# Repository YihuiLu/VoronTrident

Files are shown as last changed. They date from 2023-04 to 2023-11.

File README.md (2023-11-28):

# 一灰VoronTrident省心方案

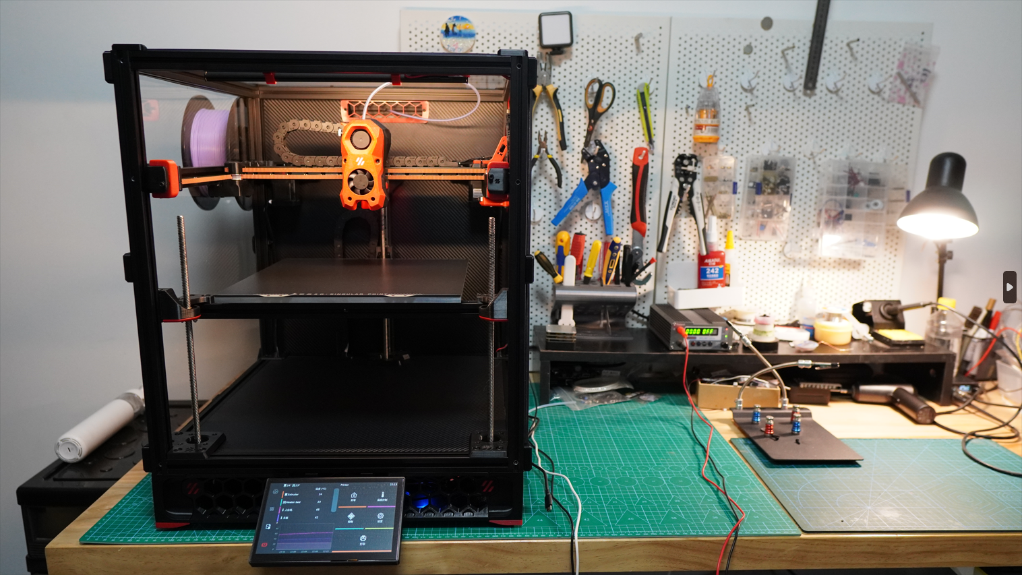
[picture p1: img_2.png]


>### **视频来源**：[Bilibili@我是小一灰](https://www.bilibili.com/video/BV1Na4y1G7fo "我是小一灰")
>### QQ交流群：940677189（满）、339148314（2群）
> ### **Gitee（国内）项目地址**：[VoronTrident省心方案](https://gitee.com/yifeilu/voron-trident "我是小一灰")
> ### **Github项目地址**：[VoronTrident省心方案](https://github.com/YihuiLu/VoronTrident "我是小一灰")

## 方案介绍：
一个被800+人选择的Voron三叉戟装配方案，所有搭配、升级方案都经过挑选和论证，也很容易买到，可以帮助你用更低的成本装出一个高性价比的Voron三叉戟，并有三个预算区间可选。

## 其他资料：
#### **中文安装文档（人工翻译）**：云盘内寻找，太大了Github传不上来

#### **BOM单**：[【腾讯文档】三叉戟BOM](https://docs.qq.com/sheet/DYk5tTHBpSEtPbVh6?tab=BB08J2 "我是小一灰")
#### **BOM单**：[【GoogleDrive】三叉戟BOM](https://drive.google.com/drive/folders/1CQs1cbmclPbKJLRexb8YkByajW4hnJqs?usp=sharing "我是小一灰")

#### **资料包下载地址1**：[阿里云盘 | 提取码：f53j](https://www.aliyundrive.com/s/3trxumG1iBN "我是小一灰")
#### **资料包下载地址2**：[百度云盘 | 提取码：ImYH](https://pan.baidu.com/s/1v2R7Pyi2rMt5dJELF42Imw?pwd=ImYH "我是小一灰")
#### **资料包下载地址3**：[一灰博客](https://drive.yifeilu.cn/aliyun/%E8%A7%86%E9%A2%91%E5%85%B1%E4%BA%AB%E6%96%87%E4%BB%B6/%E4%B8%89%E5%8F%89%E6%88%9F "我是小一灰")

#### 主板、驱动散热风扇支架：已上传至本项目"主板散热支架"文件夹。

#### 屏幕支架（百度云）：https://pan.baidu.com/s/19mTuXdeaKCQE-1kaWURAGw 提取码: 2v3t
#### 屏幕支架（GoogleDrive）：https://drive.google.com/file/d/1Th-2ryH3IjCn2Ey7RBrqZtft3pnhlUIA/view?usp=drive_link

##### - ps:中文装配文档在资料包中 -
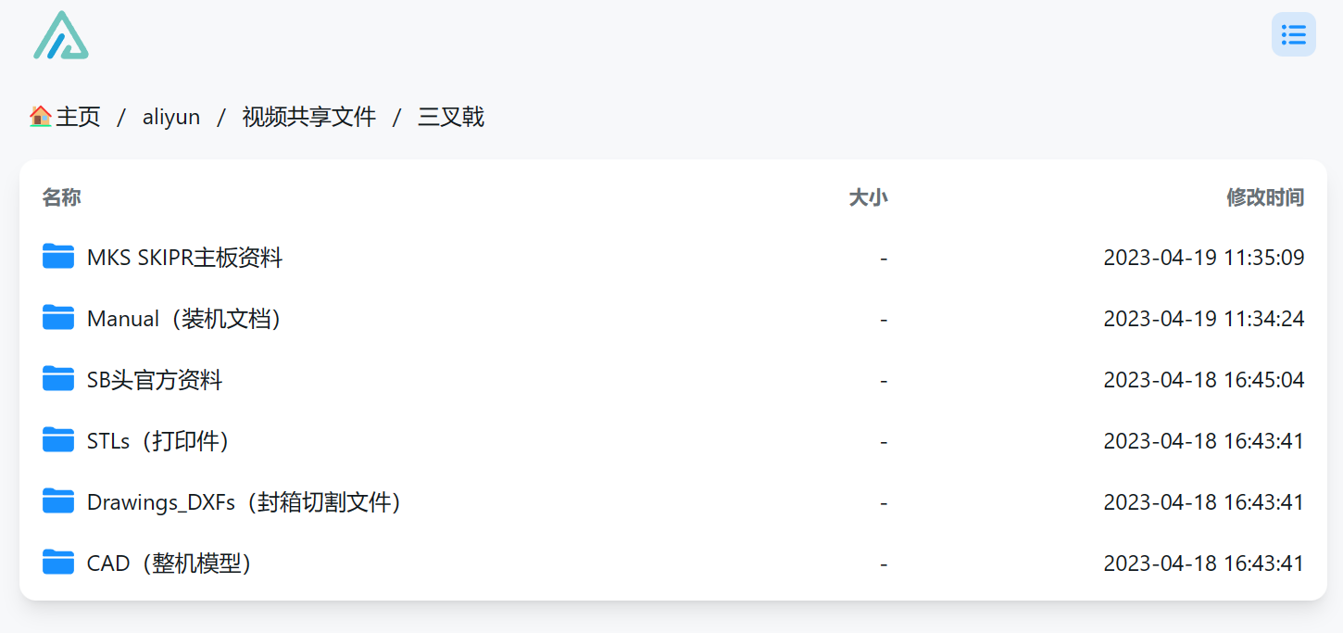
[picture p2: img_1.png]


### **方案中使用到的接线图：**

对于必趣Manta M8P V2.0主板
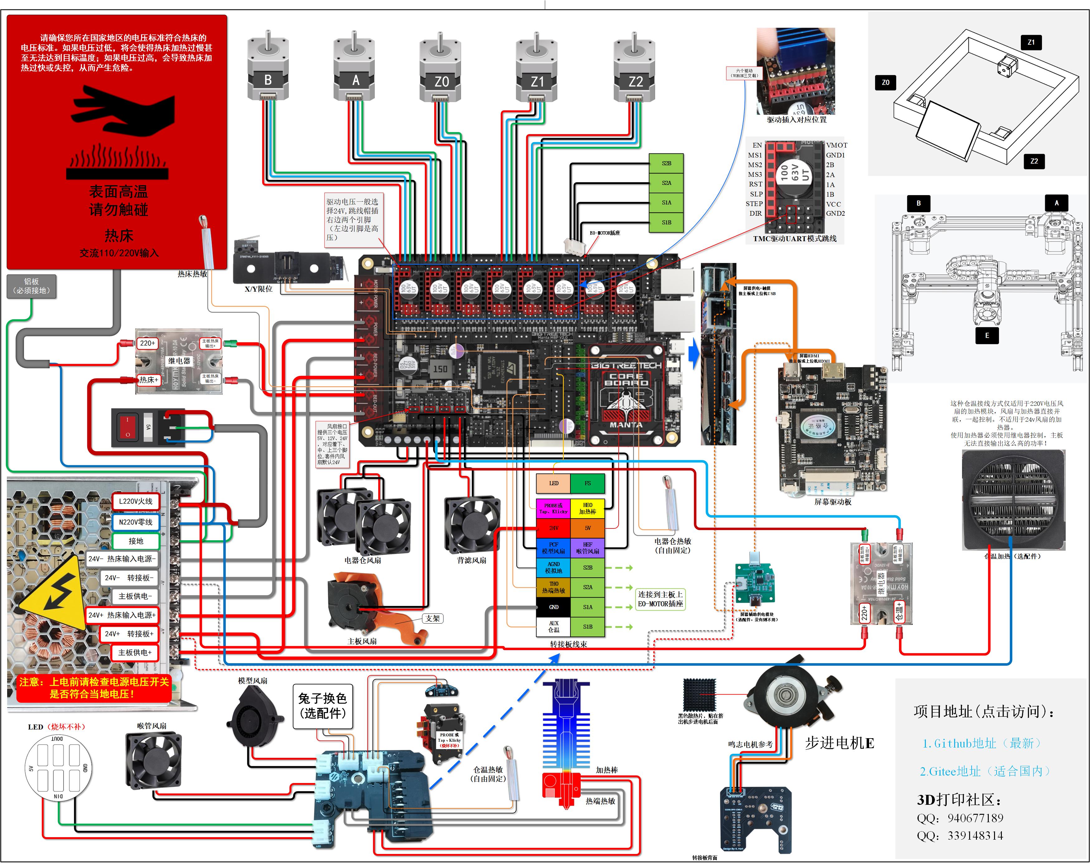
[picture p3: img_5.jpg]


对于必趣Manta M8P V1.1主板
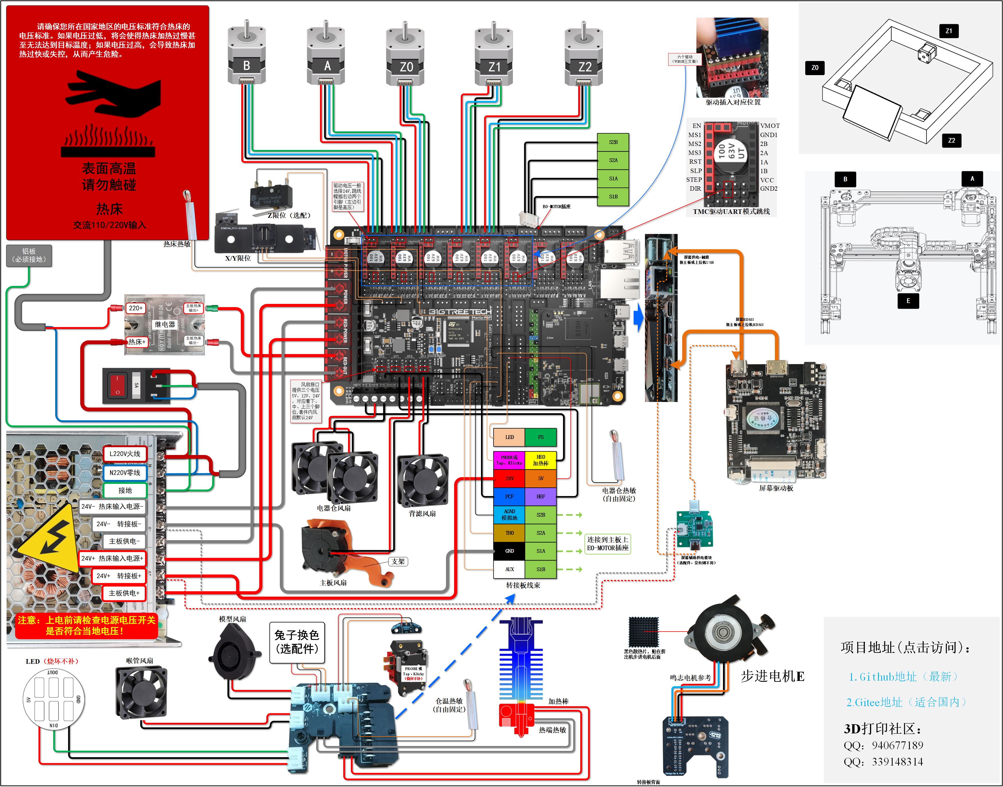
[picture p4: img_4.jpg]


对于MKS Skipr主板

#### **腾讯文档在线查看**：[Voron三叉戟接线图-Skipr](https://docs.qq.com/pdf/DYkhEa2V5WHFHUHd1? "我是小一灰")
#### **GoogleDrive在线查看**：[Voron三叉戟接线图-Skipr](https://drive.google.com/file/d/12_wtBbF1vBpWM0nNy4lV2uWEw3sMo3vR/view?usp=drive_link "我是小一灰")

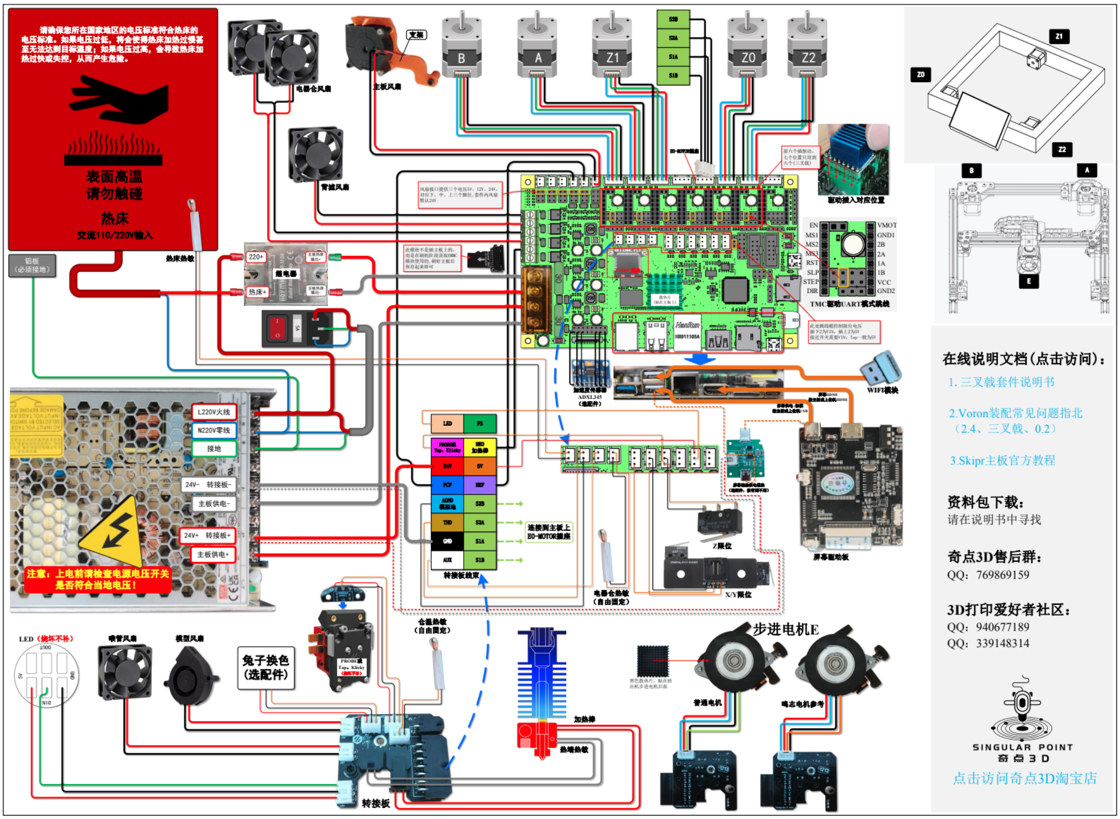
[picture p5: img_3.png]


### 注意事项：

1. 配置文件以此项目为准，可能会更新
2. 由于Git不便存储大文件，所以请结合云盘下载
3. 所有资料优先使用在线版本，离线版本更新很慢
4. 国外小伙伴若无法访问部分资料请提issue

### 其他说明：

1. 本次方案默认为300尺寸方案，而上个2400元Voron2.4的视频为250尺寸，价格不可直接对比
2. 本次方案配件质量、数量全面升级，同上，价格不可直接对比
3. 资料中的中文三叉戟组装文档为一灰自行翻译，转载请注明出处
4. 资料异常若无法联系到一灰可发邮件：yihuiwork@outlook.com

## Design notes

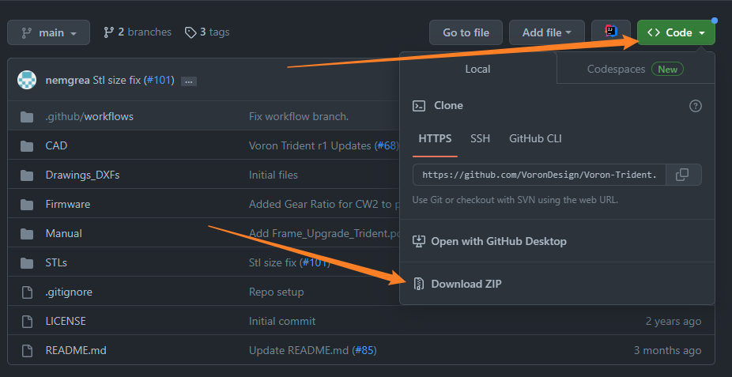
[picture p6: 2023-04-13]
img.png

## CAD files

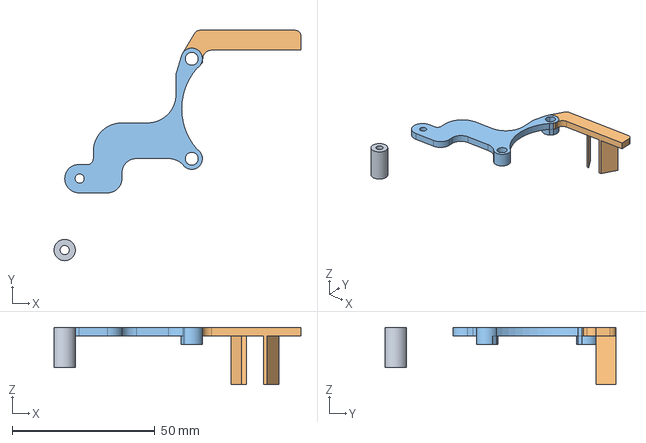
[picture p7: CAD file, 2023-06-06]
主板散热支架/skipr风扇支架(4020涡扇AB头那种).step
86.5 x 80.8 x 20.0 mm

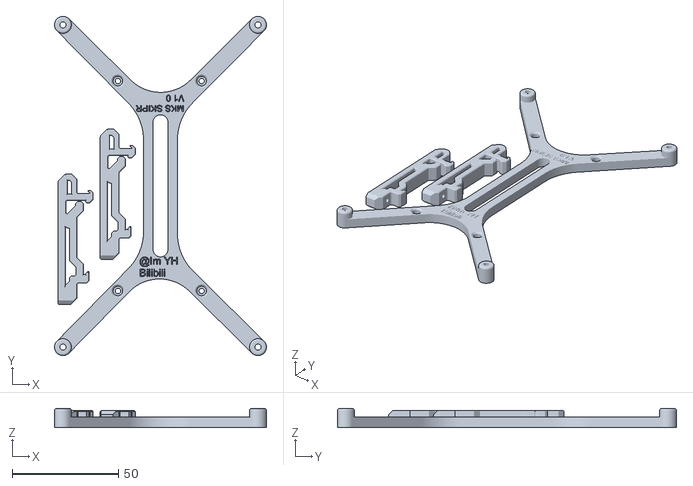
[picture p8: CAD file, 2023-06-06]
主板散热支架/Skipr主板支架-一灰.stl
100.0 x 160.0 x 9.00

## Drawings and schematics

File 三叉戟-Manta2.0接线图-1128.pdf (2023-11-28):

A | Z1
B | Z0 | Z2

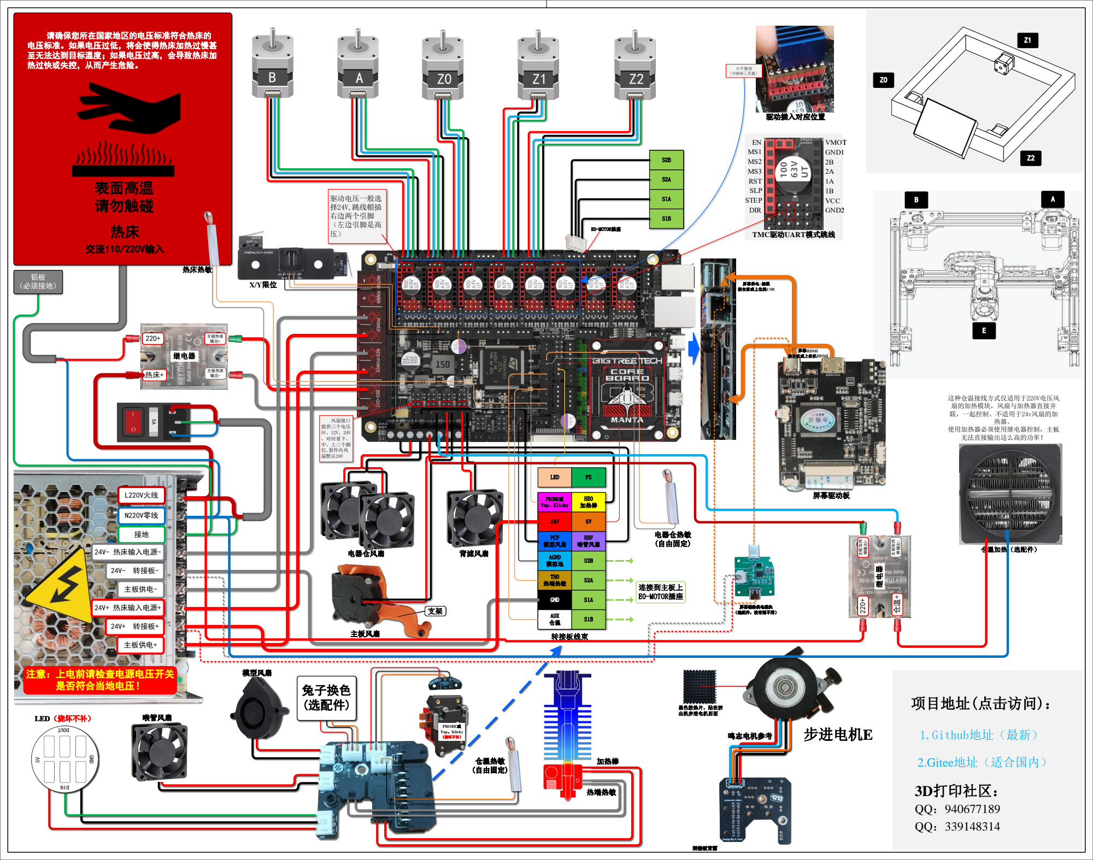
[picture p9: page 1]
主板风扇; 电器仓风扇; 背滤风扇; 继电器; 主板热床 输出+; 主板热床 输出-; 注意：上电前请检查电源电压开关 是否符合当地电压！; L220V火线; N220V零线; 主板供电-; 24V+ 转接板+; 主板供电+; 24V- 转接板-; LED; 连接到主板上 E0-MOTOR插座; E0-MOTOR插座; 表面高温 请勿触碰; 交流110/220V输入; 铝板 （必须接地）; TMC驱动UART模式跳线; 驱动电压一般选 择24V,跳线帽插 右边两个引脚 （左边引脚是高 压）; 转接板线束; 热床热敏; X/Y限位; 24V+ 热床输入电源+; 24V- 热床输入电源-; 风扇接口 提供三个电压 5V、12V、24V ，对应着下、 中、上三个脚 位,套件内风 扇默认24V; 屏幕驱动板; 屏幕辅助供电模块 （选配件，没有则不用）; 屏幕供电+触摸 接主板或上位机USB; 屏幕HDMI 接主板或上位机HDMI; 驱动插入对应位置; 电器仓热敏 (自由固定); PROBE或 Tap、Klicky （烧坏不补）; 兔子换色 (选配件); 加热棒; 热端热敏; 模型风扇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

请确保您所在国家地区的电压标准符合热床的
电压标准。如果电压过低，将会使得热床加热过慢甚
至无法达到目标温度；如果电压过高，会导致热床加
热过快或失控，从而产生危险。

PROBE或 PROBE或 PROBE或 Tap、Klicky Tap、Klicky Tap、Klicky | HE0 HE0 HE0 加热棒 加热棒 加热棒

PCF PCF PCF 模型风扇 模型风扇 模型风扇 | HEF HEF HEF 喉管风扇 喉管风扇 喉管风扇

AGND AGND AGND 模拟地 模拟地 模拟地 | S2B S2B S2B

TH0 TH0 TH0 热端热敏 热端热敏 热端热敏 | S2A S2A S2A

GND GND GND | S1A S1A S1A

AUX AUX AUX 仓温 仓温 仓温 | S1B S1B S1B

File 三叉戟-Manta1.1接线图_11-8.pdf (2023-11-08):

A | Z1
B | Z0 | Z2

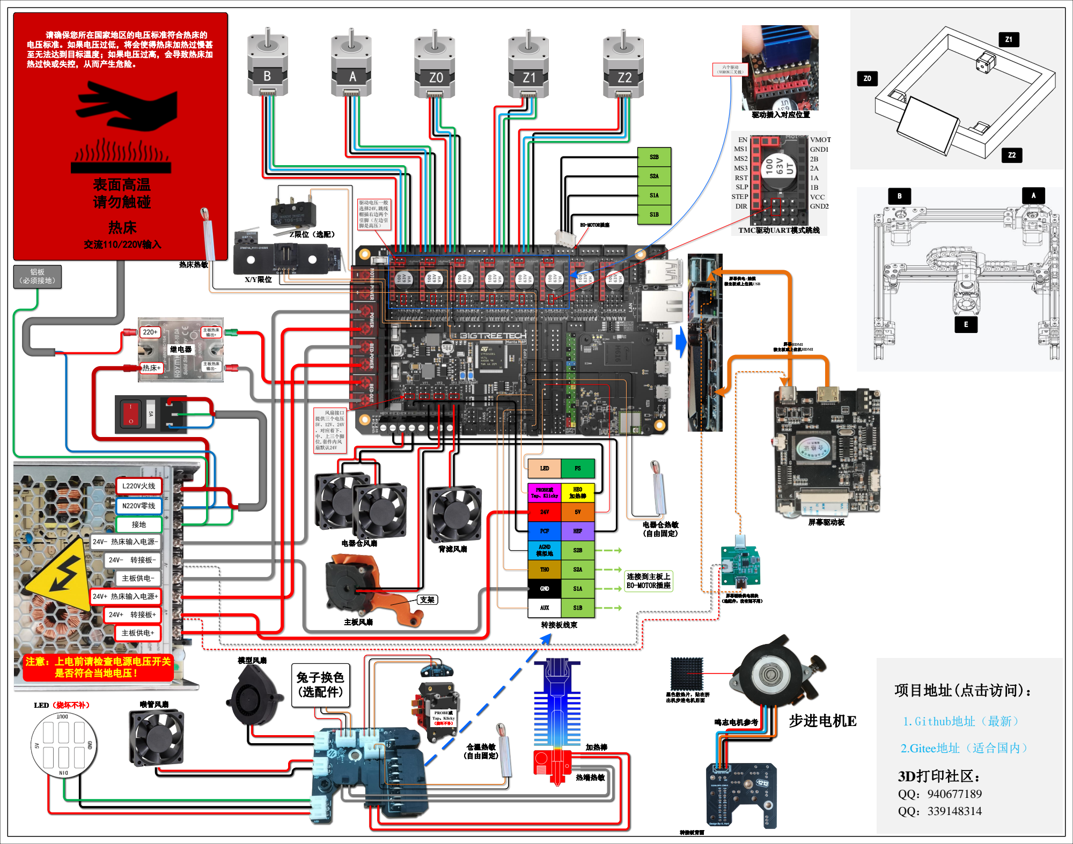
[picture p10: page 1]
主板风扇; 背滤风扇 电器仓风扇; Z限位（选配）; 继电器; 主板热床 输出+; 主板热床 输出-; 注意：上电前请检查电源电压开关 是否符合当地电压！; L220V火线; N220V零线; 主板供电-; 24V+ 转接板+; 主板供电+; 24V- 转接板-; LED; 连接到主板上 E0-MOTOR插座; E0-MOTOR插座; 表面高温 请勿触碰; 交流110/220V输入; 铝板 （必须接地）; TMC驱动UART模式跳线; 驱动电压一般 选择24V,跳线 帽插右边两个 引脚（左边引 脚是高压）; 转接板线束; 热床热敏; X/Y限位; 24V+ 热床输入电源+; 24V- 热床输入电源-; 风扇接口 提供三个电压 5V、12V、24V ，对应着下、 中、上三个脚 位,套件内风 扇默认24V; 屏幕驱动板; 屏幕辅助供电模块 （选配件，没有则不用）; 屏幕供电+触摸 接主板或上位机USB; 屏幕HDMI 接主板或上位机HDMI; 驱动插入对应位置; 电器仓热敏 (自由固定); PROBE或 Tap、Klicky （烧坏不补）; 兔子换色 (选配件); 加热棒; 热端热敏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

请确保您所在国家地区的电压标准符合热床的
电压标准。如果电压过低，将会使得热床加热过慢甚
至无法达到目标温度；如果电压过高，会导致热床加
热过快或失控，从而产生危险。

PROBE或 PROBE或 PROBE或 Tap、Klicky Tap、Klicky Tap、Klicky | HE0 HE0 HE0 加热棒 加热棒 加热棒

PCF PCF PCF | HEF HEF HEF

AGND AGND AGND 模拟地 模拟地 模拟地 | S2B S2B S2B

GND GND GND | S1A S1A S1A

AUX AUX AUX | S1B S1B S1B

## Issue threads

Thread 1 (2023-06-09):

打印中会自动关闭SB头的LED灯

smile4140, 2023-06-09:
voron三叉戟，团购套件，打印中时会自动关闭SB头的LED，好像是第一层打完就会关闭，自动关闭后，如果手动点LED的宏，可以亮一会儿又灭了，然后再点宏也不会亮了，使用的闲人拓竹切片1.6.3版本，查看了切片GCODE文件，没找到关灯的代码，应该不是切片的锅（同一切片软件，给voron2.4切片就不会有自动关灯的现象），但是打印机配置文件里也没找到会导致打印中关灯的宏或其他代码，希望能排查解决下

YihuiLu, 2023-08-03:
检查中..

NOBLE047-SIX, 2025-01-14:
同问

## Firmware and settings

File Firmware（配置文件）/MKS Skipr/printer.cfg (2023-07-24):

# This file contains common pin mappings for MKS SKIPR
# boards. To use this config, the firmware should be compiled for the
# stm32f407. When running "make menuconfig", select the 48KiB
# bootloader, and enable "Serial for communication" and select the "on USART1 PA10/PA9"

# The "make flash" command does not work on the MKS SKIPR. Instead,
# after running "make", copy the generated "out/klipper.bin" file to a
# file named "mks_skipr.bin" on an SD card and then restart the
# MKS SKIPR with that SD card.

# See docs/Config_Reference.md for a description of parameters.

##===================以上内容为MKS官方注释，保留选择阅读==================================

## 此配置文件为Voron三叉戟制作，使用MKS Skipr V1.0主板
## @我是小一灰
## Bilibili（视频地址）：https://space.bilibili.com/258313383
## 项目地址：https://github.com/YihuiLu/VoronTrident
## 资料地址：https://www.aliyundrive.com/s/3trxumG1iBN  提取码: f53j
## QQ交流群：940677189（1群满）、339148314（2群）
##
## 使用方法：
## 1. 首先保证接线正确，按线管文字和接线图提示操作，在操作此文件前你的打印机应该能够正常开机并联网
## 2. 将此文件以及文件夹内其他配置文件上传至Fluidd配置文件目录
## 3. 根据你的打印机尺寸，将提示需要取消注释的部分取消注释，将不属于你的尺寸部分注释掉
## 4. 进行PID校准  参考：https://www.bilibili.com/read/cv20977348
## 5. 校准挤出距离 参考：https://www.klipper3d.org/zh/Rotation_Distance.html
## 6. 进行Z补偿 如果是Tap参考：https://www.bilibili.com/video/BV1x3411Z7Wg，如果是接近开关参考：https://www.bilibili.com/read/cv20808316
##
## 注意事项：
## 1. 使用Skipr主板MCU部分建议使用USB通信模式，教程 https://docs.qq.com/doc/DYk56dkpVcWl4SGJO
## 2. 严格保持代码格式，注意中英文字符区别
## 3. 使用电脑浏览器打开控制台编辑此文件，有利于保持格式

##==================================================================================.
# [include mainsail.cfg]
[include fluidd.cfg] # 引入配置文件，部分配置在这个文件里
[include stealthburner_leds.cfg] # LED配置，如果没导入stealthburner_leds.cfg这个配置文件，会报错

[mcu] # 连接下位机配置，不懂不要修改
# The hardware use USART1 PA10/PA9 connect to RK3328
# 注意！！！，这个方式是官方默认的UART连接方式，不适合高速打印和挂载外接设备
# 建议参考这个方案优化：【腾讯文档】Skipr改USB教程 https://docs.qq.com/doc/DYk56dkpVcWl4SGJO
# serial: /dev/serial/by-id/usb-Klipper_stm32f407xx_2B0032000350464732383020-if00
serial: /dev/ttyS0
restart_method: command

[mcu rpi]
serial: /tmp/klipper_host_mcu

[printer] # 机型声明
kinematics: corexy
max_velocity: 200
max_accel: 12000
max_z_velocity: 15
max_z_accel: 100
square_corner_velocity: 5.0

#####################################################################
# 	X/Y 电机设置
#####################################################################

[stepper_x]
step_pin:PC14
dir_pin:!PC13
enable_pin:!PC15
microsteps: 16
rotation_distance: 40
full_steps_per_rotation:200  #set to 400 for 0.9 degree stepper
endstop_pin:PA14
position_min: 0
homing_speed: 35   #Max 100
homing_retract_dist: 5
homing_positive_dir: true
step_pulse_duration:0.000002  # 不要修改

##	250尺寸取消以下注释
#position_endstop: 250
#position_max: 250

##	300尺寸取消以下注释
position_endstop: 300
position_max: 300

##	350尺寸取消以下注释
#position_endstop: 350
#position_max: 350


[tmc2209 stepper_x]
uart_pin: PE6
run_current: 1.1
# hold_current: 0.2
# interpolate: True  # 开启插补
# stealthchop_threshold: 400  # 静音


[stepper_y]
step_pin:PE5
dir_pin:!PE4
enable_pin:!PD14
microsteps:16
rotation_distance: 40
full_steps_per_rotation:200  #set to 400 for 0.9 degree stepper
endstop_pin:PA15
position_min: 0
homing_speed:35
homing_retract_dist:5
homing_positive_dir:true
step_pulse_duration:0.000002  # 不要修改
##--------------------------------------------------------------------
##	Uncomment for 250mm build
#position_endstop: 250
#position_max: 250

##	Uncomment for 300mm build
position_endstop: 306
position_max: 306

##	Uncomment for 350mm build
#position_endstop: 350
#position_max: 350
##--------------------------------------------------------------------


[tmc2209 stepper_y]
uart_pin: PE3
run_current: 1.1
# hold_current: 0.2
# interpolate: True
# stealthchop_threshold: 400


#####################################################################
# 	Z 电机配置
#####################################################################

# Z0 电机为左前
[stepper_z]
step_pin:PD6
dir_pin:PD5
enable_pin:!PD7
microsteps: 16
##T8x8导螺杆。旋转一圈可移动床8mm
##根据实际情况修改，套件按官方BOM采购默认导程8
#rotation_distance: 8 # 如果你使用导程8的丝杆则取消注释此项，并注释上一行，三个轴都要这么操作
rotation_distance: 4 # 暂用4
full_steps_per_rotation: 200
endstop_pin: probe:z_virtual_endstop # 如果你不使用tap，则修改此配置
#  Z-position of nozzle (in mm) to z-endstop trigger point relative to print surface (Z0)
#  (+) value = endstop above Z0, (-) value = endstop below
#  Increasing position_endstop brings nozzle closer to the bed
#  After you run Z_ENDSTOP_CALIBRATE, position_endstop will be stored at the very end of your config
#position_endstop: 2 #如果不使用Tap，修改此处
## All builds use same Max Z
position_max: 250
position_max: 250
position_min: -5
homing_speed: 35.0
step_pulse_duration:0.000002  # 不要修改

# z补偿校准命令：（对于使用Tap的用户）
# PROBE_CALIBRATE
# 输入后，进行A4纸测量就行


[tmc2209 stepper_z]
uart_pin: PB7
run_current: 0.8
hold_current: 0.5
# interpolate: True
stealthchop_threshold: 999999 # 999999意味着开启静音模式


# Z1 后部电机
[stepper_z1]
step_pin:PE1
dir_pin:PE0
enable_pin: !PE2
microsteps: 16
#rotation_distance: 8 # 如果你使用导程8的丝杆则取消注释此项，并注释上一行，三个轴都要这么操作
rotation_distance: 4 # 暂用4
full_steps_per_rotation: 200
step_pulse_duration:0.000002  # 不要修改

[tmc2209 stepper_z1]
uart_pin: PD4
interpolate: True
run_current: 0.8
hold_current: 0.5
# interpolate: True
stealthchop_threshold: 999999 # 999999意味着开启静音模式

# z2电机右前
[stepper_z2]
step_pin:PD2
dir_pin:PD1
enable_pin:!PD3
microsteps: 16
#rotation_distance: 8 # 如果你使用导程8的丝杆则取消注释此项，并注释上一行，三个轴都要这么操作
rotation_distance: 4 # 暂用4
full_steps_per_rotation: 200
step_pulse_duration:0.000002  # 不要修改

[tmc2209 stepper_z2]
uart_pin: PD0
run_current: 0.8
hold_current: 0.5
# interpolate: True
stealthchop_threshold: 999999 # 999999意味着开启静音模式


#####################################################################
# 挤出机
#####################################################################
[extruder]
step_pin:!PB5
dir_pin:!PB4
enable_pin:!PB6
microsteps: 16
# Tune per individual printer
# Default for Bondtech 5mm Bore Drive Gears
##执行挤出机校准时更新以下值
##算法：比如你挤出100mm的耗材，但实际上是98毫米：
##那么rotation_distance=<当前rotation_distance值>*<实际挤出长度>/100
rotation_distance: 13.6255
full_steps_per_rotation: 200
gear_ratio: 50:17
nozzle_diameter: 0.400
filament_diameter: 1.750
#pressure_advance: 0.67
#pressure_advance_smooth_time: 0.040
heater_pin: PB1
##	Validate the following thermistor type to make sure it is correct
sensor_type: Generic 3950
#   Type of sensor - common thermistors are "EPCOS 100K B57560G104F",
#   "ATC Semitec 104GT-2", "ATC Semitec 104NT-4-R025H42G", "Generic
#   3950","Honeywell 100K 135-104LAG-J01", "NTC 100K MGB18-104F39050L32",
#   "SliceEngineering 450", and "TDK NTCG104LH104JT1". See the
#   "Temperature sensors" section for other sensors. This parameter
#   must be provided.
sensor_pin: PC3
min_extrude_temp: 175
min_temp: 0
max_temp: 300
step_pulse_duration:0.000002  # 不要修改
#control = pid
#pid_kp = 26.213
#pid_ki = 1.304
#pid_kd = 131.721


[tmc2208 extruder]
uart_pin: PB3
run_current: 0.6
# hold_current: 0.2
# sense_resistor: 0.110
# stealthchop_threshold: 0


#####################################################################
#  热床
#####################################################################
[heater_bed]
heater_pin: PD12
##  Choose the correct thermistor for your heater
sensor_type: Generic 3950
sensor_pin: PC0
##	Adjust Max Power so your heater doesn't warp your bed
max_power: 0.9
min_temp: 0
max_temp: 120
#control: pid
#pid_kp: 58.437
#pid_ki: 2.347
#pid_kd: 363.769

#####################################################################
# 	探头
#####################################################################

[probe]
pin:PB15
x_offset: 0 # tap为0
y_offset: 0 # tap为0
#z_offset: 0
speed: 10
samples: 3
samples_result: median
sample_retract_dist: 5.0
samples_tolerance: 0.09
samples_tolerance_retries: 3

activate_gcode:  # 不使用tap则删除此部分
    {% set PROBE_TEMP = 150 %}
    {% set MAX_TEMP = PROBE_TEMP + 5 %}
    {% set ACTUAL_TEMP = printer.extruder.temperature %}
    {% set TARGET_TEMP = printer.extruder.target %}

    {% if TARGET_TEMP > PROBE_TEMP %}
        { action_respond_info('挤出机目标温度过高: %.1fC , 等待降低至: %.1fC' % (TARGET_TEMP, PROBE_TEMP)) }
        M109 S{ PROBE_TEMP }
        STATUS_HEATING
    {% else %}
        # Temperature target is already low enough, but nozzle may still be too hot.
        {% if ACTUAL_TEMP > MAX_TEMP %}
            { action_respond_info('挤出机温度仍然太高 %.1fC , 等待降低至: %.1fC' % (ACTUAL_TEMP, MAX_TEMP)) }
            TEMPERATURE_WAIT SENSOR=extruder MAXIMUM={ MAX_TEMP }
        {% endif %}
    {% endif %}
    # M109 S{ TARGET_TEMP }
    STATUS_LEVELING

#####################################################################
# 	风扇
#####################################################################
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

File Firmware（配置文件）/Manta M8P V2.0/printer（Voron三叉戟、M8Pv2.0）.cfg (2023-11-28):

# This file contains common pin mappings for the BIGTREETECH Manta M8P
# To use this config, the firmware should be compiled for the
# STM32G0B1 with a "8KiB bootloader" and USB communication.

# See docs/Config_Reference.md for a description of parameters.
##===================以上内容为M8P官方注释，保留选择阅读==================================

## 此配置文件为Voron三叉戟制作，使用必趣Manta M8P V2.0主板
## @我是小一灰
## Bilibili（视频地址）：https://space.bilibili.com/258313383
## 项目地址：https://github.com/YihuiLu/VoronTrident
## 接线图：项目内查找
## 资料地址：项目内查找
## QQ交流群：940677189（1群满）、339148314（2群）
##
## 使用方法：
## 1. 首先保证接线正确，按线管文字和接线图提示操作，在操作此文件前你的打印机应该能够正常开机并联网
## 2. 将此文件以及文件夹内其他配置文件上传至Fluidd配置文件目录
## 3. 根据你的打印机尺寸，将提示需要取消注释的部分取消注释，将不属于你的尺寸部分注释掉
## 4. 进行PID校准  参考：https://www.bilibili.com/read/cv20977348
## 5. 校准挤出距离 参考：https://www.klipper3d.org/zh/Rotation_Distance.html
## 6. 进行Z补偿 如果是Tap参考：https://www.bilibili.com/video/BV1x3411Z7Wg，如果是接近开关参考：https://www.bilibili.com/read/cv20808316
##
## 注意事项：
## 1. 确保此配置文件与你的主板型号一致
## 2. 严格保持代码格式，注意中英文字符区别
## 3. 使用电脑浏览器打开控制台编辑此文件，有利于保持格式

##==================================================================================.
[include mainsail.cfg]
[include stealthburner_leds.cfg] # LED配置，如果没导入stealthburner_leds.cfg这个配置文件，会报错
[mcu]

##--------------------------------------------------------------------
serial: /dev/serial/by-id/usb-Klipper_stm32h723xx_440016000D51313236343430-if00
#restart_method: command
##--------------------------------------------------------------------

[printer] # 机型声明
kinematics: corexy
max_velocity: 200
max_accel: 6000
max_z_velocity: 15 			#Max 15 for 12V TMC Drivers, can increase for 24V
max_z_accel: 100
square_corner_velocity: 5.0

[temperature_sensor MCU]
sensor_type: temperature_mcu

[temperature_sensor SoC]
sensor_type: temperature_host

#####################################################################
# 	X/Y 电机配置
#####################################################################

## X Stepper on Motor1(B Motor)
[stepper_x]
step_pin: PE6
dir_pin: PE5
enable_pin: !PC14
microsteps: 16
rotation_distance: 40
endstop_pin: ^PF4
position_min: 0

##--------------------------------------------------------------------
##	250尺寸取消以下注释
#position_endstop: 250
#position_max: 250

##	300尺寸取消以下注释
position_endstop: 300
position_max: 300

##	350尺寸取消以下注释
#position_endstop: 350
#position_max: 350

##--------------------------------------------------------------------
homing_speed: 50   #Max 100
homing_retract_dist: 5
homing_positive_dir: true

##	Make sure to update below for your relevant driver (2208 or 2209)
[tmc2209 stepper_x]
uart_pin: PC13
interpolate: True
run_current: 1.1
hold_current: 0.5
sense_resistor: 0.110
stealthchop_threshold: 999999

## Y Stepper on Motor2 (A Motor)
[stepper_y]
step_pin: PE2
dir_pin: PE1
enable_pin: !PE4
microsteps: 16
rotation_distance: 40
endstop_pin: ^PF3
position_min: 0
##--------------------------------------------------------------------

##	250尺寸取消以下注释
#position_endstop: 250
#position_max: 250

##	300尺寸取消以下注释
position_endstop: 300
position_max: 300

##	350尺寸取消以下注释
#position_endstop: 350
#position_max: 350

##--------------------------------------------------------------------
homing_speed: 50  #Max 100
homing_retract_dist: 5
homing_positive_dir: true

##	Make sure to update below for your relevant driver (2208 or 2209)
[tmc2209 stepper_y]
uart_pin: PE3
interpolate: True
run_current: 1.1
hold_current: 0.5
sense_resistor: 0.110
stealthchop_threshold: 999999

#####################################################################
# 	Z 电机配置
#####################################################################
## Z0电机为左前
[stepper_z]
step_pin: PB8
dir_pin: !PB7
enable_pin: !PE0
microsteps: 16
#rotation_distance: 8 # 如果你使用导程8的丝杆则取消注释此项，并注释上一行，三个轴都要这么操作
rotation_distance: 4 # 暂用4
full_steps_per_rotation: 200
#endstop_pin: ^PF5
##  Z-position of nozzle (in mm) to z-endstop trigger point relative to print surface (Z0)
##  (+) value = endstop above Z0, (-) value = endstop below
##	Increasing position_endstop brings nozzle closer to the bed
##  After you run Z_ENDSTOP_CALIBRATE, position_endstop will be stored at the very end of your config
#position_endstop: -0.5
endstop_pin: probe:z_virtual_endstop
##--------------------------------------------------------------------
##	250尺寸取消以下注释
#position_max: 240

##	300尺寸取消以下注释
position_max: 290

##	350尺寸取消以下注释
#position_max: 350
##--------------------------------------------------------------------
position_min: -4
homing_speed: 15
second_homing_speed: 3
homing_retract_dist: 3

##	Make sure to update below for your relevant driver (2208 or 2209)
[tmc2209 stepper_z]
uart_pin: PB9
interpolate: true
run_current: 0.8
hold_current: 0.4
sense_resistor: 0.110
stealthchop_threshold: 999999

# Z1 后部电机
[stepper_z1]
step_pin: PB4
dir_pin: !PB3
enable_pin: !PB6
microsteps: 16
#rotation_distance: 8 # 如果你使用导程8的丝杆则取消注释此项，并注释上一行，三个轴都要这么操作
rotation_distance: 4 # 暂用4
full_steps_per_rotation: 200

##	Make sure to update below for your relevant driver (2208 or 2209)
[tmc2209 stepper_z1]
uart_pin: PB5
interpolate: true
run_current: 0.8
hold_current: 0.5
sense_resistor: 0.110
stealthchop_threshold: 999999

# z2电机右前
[stepper_z2]
step_pin: PG13
dir_pin: !PG12
enable_pin: !PG15
microsteps: 16
#rotation_distance: 8 # 如果你使用导程8的丝杆则取消注释此项，并注释上一行，三个轴都要这么操作
rotation_distance: 4 # 暂用4
full_steps_per_rotation: 200


##	Make sure to update below for your relevant driver (2208 or 2209)
[tmc2209 stepper_z2]
uart_pin: PG14
interpolate: true
run_current: 0.8
hold_current: 0.4
sense_resistor: 0.110
stealthchop_threshold: 999999

#####################################################################
# 	挤出机配置
#####################################################################
#	E0 on Motor6
[extruder]
step_pin: PG9
dir_pin: PD7
enable_pin: !PG11
##	Update value below when you perform extruder calibration
##	If you ask for 100mm of filament, but in reality it is 98mm:
##	rotation_distance = <previous_rotation_distance> * <actual_extrude_distance> / 100
##  22.6789511 is a good starting point
rotation_distance: 22.6789511	#Bondtech 5mm Drive Gears
##	Update Gear Ratio depending on your Extruder Type
##	Use 50:17 for Afterburner/Clockwork (BMG Gear Ratio)
##	Use 80:20 for M4, M3.1
gear_ratio: 50:17				#BMG Gear Ratio
microsteps: 16
full_steps_per_rotation: 200	#200 for 1.8 degree, 400 for 0.9 degree
nozzle_diameter: 0.400
filament_diameter: 1.75
heater_pin: PA0
##	Validate the following thermistor type to make sure it is correct
sensor_type: ATC Semitec 104GT-2
sensor_pin: PB0
min_temp: -199
max_temp: 270
max_power: 1.0
min_extrude_temp: 170

#control = pid
#pid_kp = 26.213
#pid_ki = 1.304
#pid_kd = 131.721
##	Try to keep pressure_advance below 1.0
pressure_advance: 0.05
##	Default is 0.040, leave stock
pressure_advance_smooth_time: 0.040

##	E0 on Motor7
##	Make sure to update below for your relevant driver (2208 or 2209)
[tmc2209 extruder]
uart_pin: PG10
interpolate: false
run_current: 0.5
hold_current: 0.4
sense_resistor: 0.110
stealthchop_threshold: 0

#[filament_switch_sensor material_0]
#switch_pin: PC1

#[filament_switch_sensor material_1]
#switch_pin: PC2

#####################################################################
# 	热床
#####################################################################
[heater_bed]
##	SSR Pin - BED_OUT
heater_pin: PF5
sensor_type: Generic 3950
sensor_pin: PB1
##	Adjust Max Power so your heater doesn't warp your bed
max_power: 1.0
min_temp: 0
max_temp: 120
#control: pid
#pid_kp: 58.437
#pid_ki: 2.347
#pid_kd: 363.769

#####################################################################
# 	Probe探头
#####################################################################
[probe]
##	Inductive Probe
##	This probe is not used for Z height, only Quad Gantry Leveling
##  NPN and PNP proximity switch types can be set by jumper
pin: PF2
x_offset: 0
y_offset: 0
#z_offset: 0
speed: 5
samples: 3
samples_result: median
sample_retract_dist: 5.0
samples_tolerance: 0.09
samples_tolerance_retries: 3
activate_gcode:  # 不使用tap则删除此部分
    {% set PROBE_TEMP = 150 %}
    {% set MAX_TEMP = PROBE_TEMP + 5 %}
    {% set ACTUAL_TEMP = printer.extruder.temperature %}
    {% set TARGET_TEMP = printer.extruder.target %}

    {% if TARGET_TEMP > PROBE_TEMP %}
        { action_respond_info('挤出机目标温度过高: %.1fC , 等待降低至: %.1fC' % (TARGET_TEMP, PROBE_TEMP)) }
        M109 S{ PROBE_TEMP }
        STATUS_HEATING
    {% else %}
        # Temperature target is already low enough, but nozzle may still be too hot.
        {% if ACTUAL_TEMP > MAX_TEMP %}
            { action_respond_info('挤出机温度仍然太高 %.1fC , 等待降低至: %.1fC' % (ACTUAL_TEMP, MAX_TEMP)) }
            TEMPERATURE_WAIT SENSOR=extruder MAXIMUM={ MAX_TEMP }
        {% endif %}
    {% endif %}
    # M109 S{ TARGET_TEMP }
    STATUS_LEVELING
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

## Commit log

2023-04-13 初始化项目
    [printer.cfg, stealthburner_leds.cfg]
2023-04-13 优化格式
2023-04-19 补充说明
2023-04-19 优化配置文件
    [printer.cfg]
2023-05-04 优化描述
2023-05-06 增加百度云盘路径
2023-05-11 增加GoogleDrive路径
2023-06-06 修正一些错误
    [printer.cfg]
2023-06-06 补充一些资料
    [Skipr主板支架-一灰.stl, skipr风扇支架(4020涡扇AB头那种).step]
2023-06-13 微调参数
    [printer.cfg]
2023-06-21 补充资料
2023-06-23 优化配置
    [printer.cfg]
2023-08-03 增加必趣M8P配置文件和接线图
    [printer.cfg, printer（Voron三叉戟,M8P）.cfg, stealthburner_leds.cfg]
2023-08-08 增加中文文档位置描述
2023-08-08 将配置文件从M8P V1.0 升级为2.0
    [printer（Voron三叉戟,M8P）.cfg, stealthburner_leds.cfg]
2023-10-23 修改M8P主板z配置错误
    [printer（Voron三叉戟,M8P）.cfg]
2023-11-08 修改接线图中存在的一些BUG
2023-11-08 传错pdf了
2023-11-14 修改一些不合理的配置参数
    [printer（Voron三叉戟,M8P）.cfg]
2023-11-28 增加对必趣M8P V2.0主板的支持，增加舱温加热模块
    [printer（Voron三叉戟,M8P）.cfg, printer（Voron三叉戟、M8Pv2.0）.cfg, stealthburner_leds.cfg]
